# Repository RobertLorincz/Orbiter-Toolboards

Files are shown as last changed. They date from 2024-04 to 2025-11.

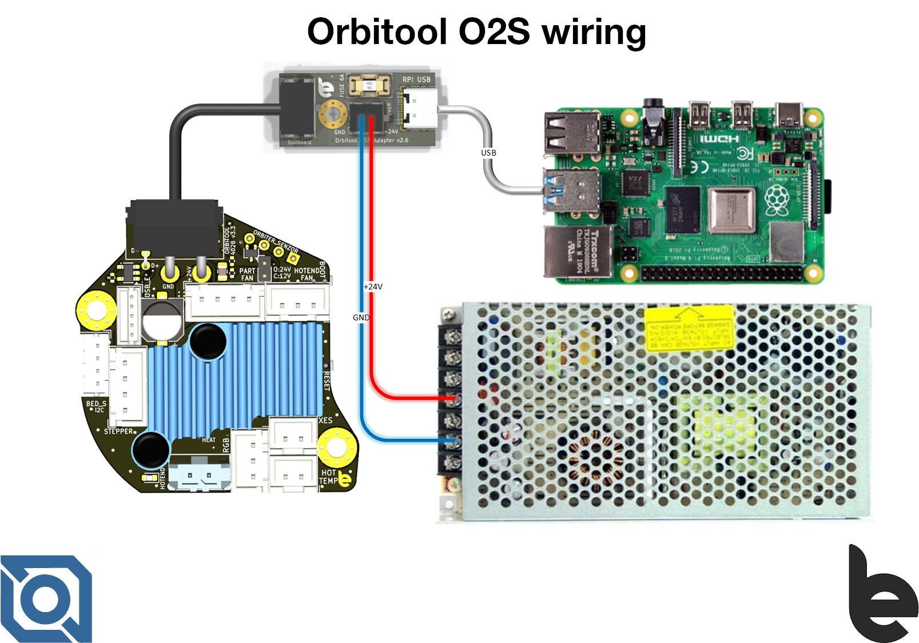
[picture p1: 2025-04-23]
Orbiter O2S Toolboard/Documentations/Orbitool O2S Wiring.jpg

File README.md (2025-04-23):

Should a tool-board magic smoke come out because of user error? Why?

Should a tool-board be destroyed by a fault in your 3D printer? Why?

My answer is NO! And this is what this tool-board is all about! 

We are hobbits, professionals and let’s face it, we do mistakes, and when the magic smoke shows up everybody is disappointed, even if we know it’s a user fault. In this board, I promise you the magic smoke is kept inside extremely tight!

Some of the main features:

•	Optimized for Orbiter v2, v2.5 and SO3 shape and features including orbiter sensor

•	STM32F042 / STM32F072 microcontroller running on 48MHz

•	Automotive USB communication with Raspberry PI

•	Onboard LIS2DW12 /ADXL345 accelerometer

•	TMC2209 extruder stepper driver

•	Direct connection to Orbiter v2 sensor

•	PWM controlled fan outputs

•	DC-DC converter based Hot-end fan driver, compatible with 12/24V fan types with RPM speed input signal

•	Hot-end temperature sensor input compatible with standard NTC or PT1000 temperature sensor types

•	I/O for bed level sensing

•	X-Stop sensor input

•	RGB LED driver output

•	Onboard temperature sensor

•	Advanced thermal management system

GOFUuGBbQAESqu3 (1)
O2 Toolboard
Orbitool USB Adapter housing

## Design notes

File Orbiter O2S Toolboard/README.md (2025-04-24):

This is the second revised version of the Orbiter O2 toolboard.

Some of the main features:

•	Optimized for Orbiter v2, v2.5 shape and features, including orbiter sensor

•	STM32F072 microcontroller running on 48MHz - full klipper support with automatic update possibility

•	Automotive USB communication with Raspberry PI

•	One auxiliary USB connector for bed scanner, nozzle camera, or other inteligent USB connected accessory

•	Onboard ADXL345 accelerometer

•	TMC2240 extruder stepper driver - for better thermal behavior

•	Direct connection to Orbiter v2 sensor

•	PWM 4,3,2 wire part fan output, compatible with 12/24V fan types with RPM speed input signal

•	DC-DC converter based Hot-end fan driver, compatible with 12/24V fan types with RPM speed input signal

•	Hot-end temperature sensor input compatible with standard NTC or PT1000 temperature sensor types

•	I2C for bed level sensing and scanning

•	X-Stop sensor input

•	RGB LED driver output

•	Onboard temperature sensor

•	Advanced thermal management system

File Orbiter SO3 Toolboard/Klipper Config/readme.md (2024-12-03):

Changes v2.2.6
- print cancel restores the printer idle timer to 10 min

Changes v2.2.5

- Included CANCEL macro for user using the sensor macros instead of their own macros
- Pausing printer due to runnout detection increases printer timeout to 3600s - 1h (configurable by pause_timeout); timeout set back to default ten minutes after print resume.
- improved temperature restore behavior
- Filament automatic unload after runnout can be disabled by variable disable_runout_unload.
- corrected some minor bugs and spelling
- messages sent to console shows SO3: prefix
- corrected RGB led incorrect color status for some failure cases

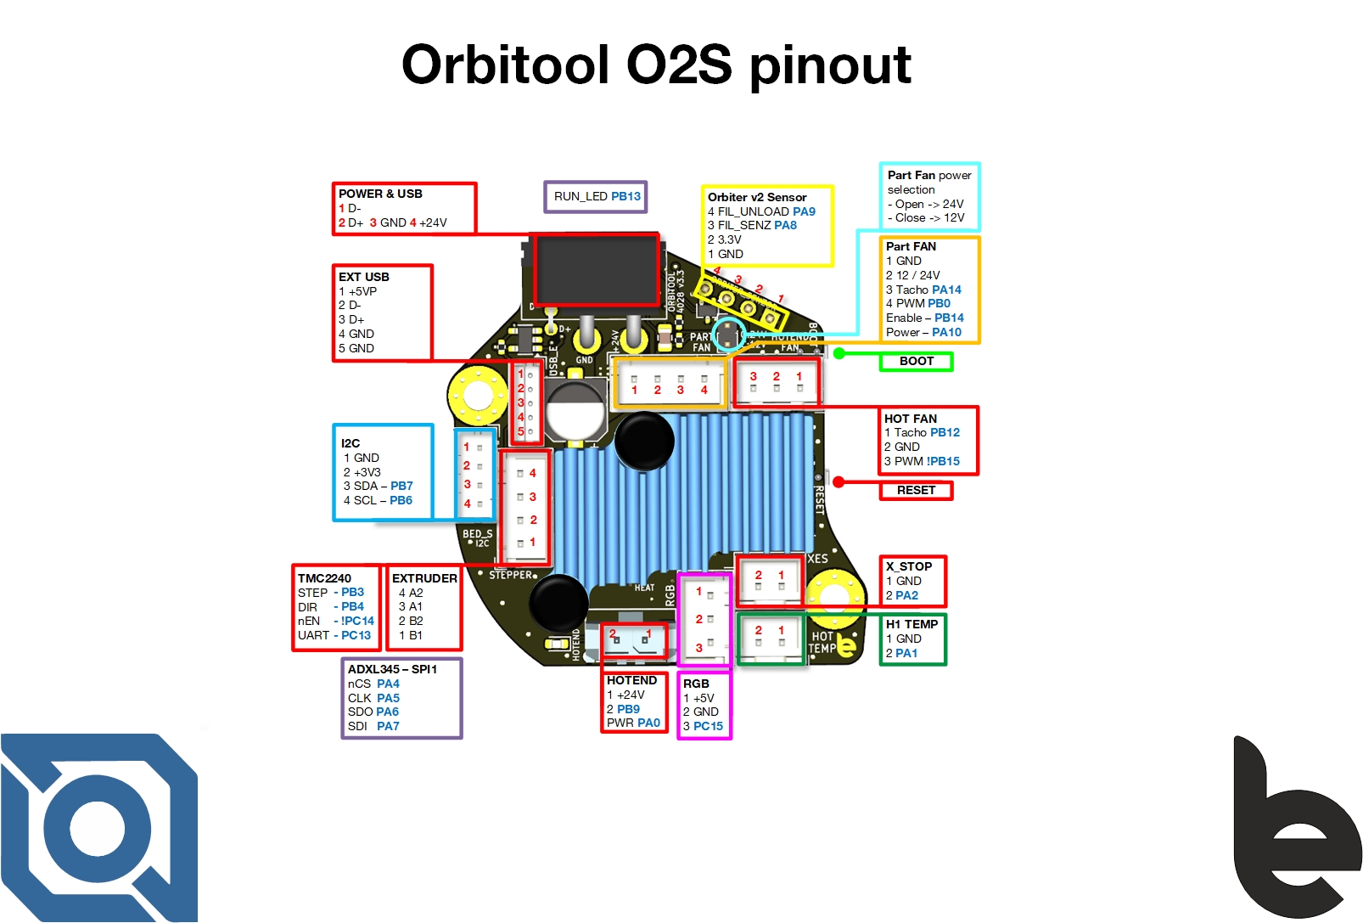
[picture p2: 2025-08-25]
Orbiter O2S Toolboard/Documentations/Orbitool O2S Pinout.jpg

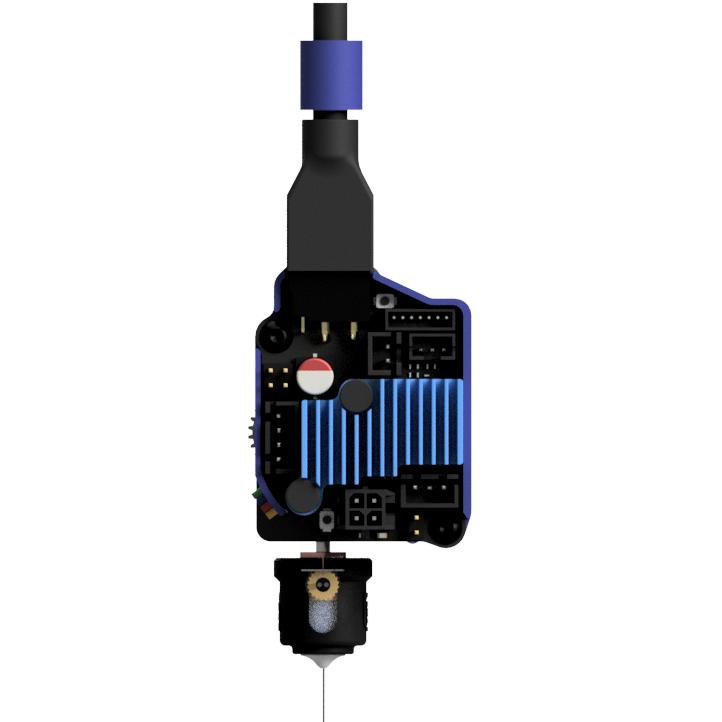
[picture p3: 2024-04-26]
Orbiter SO3 Toolboard/Pictures/Orbiter Smart LDO p3.png

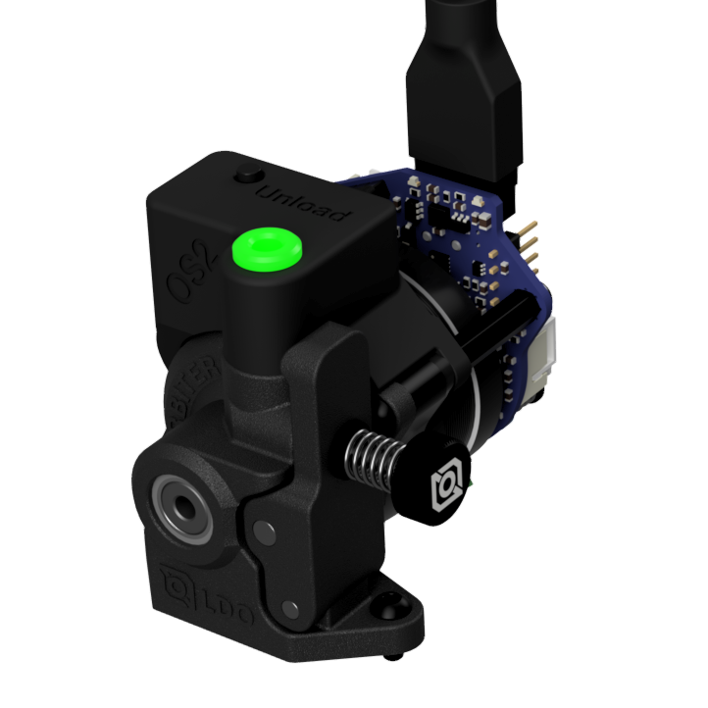
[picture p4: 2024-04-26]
Orbiter O2 Toolboard/Pictures/Orbiter v2 Toolboard v2.72 v151.png

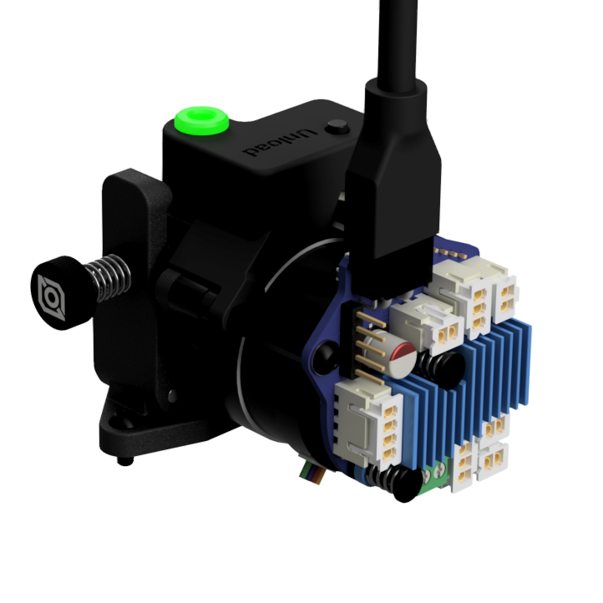
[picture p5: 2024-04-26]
Orbiter O2 Toolboard/Pictures/Orbiter v2 Toolboard v2.72 v15.png

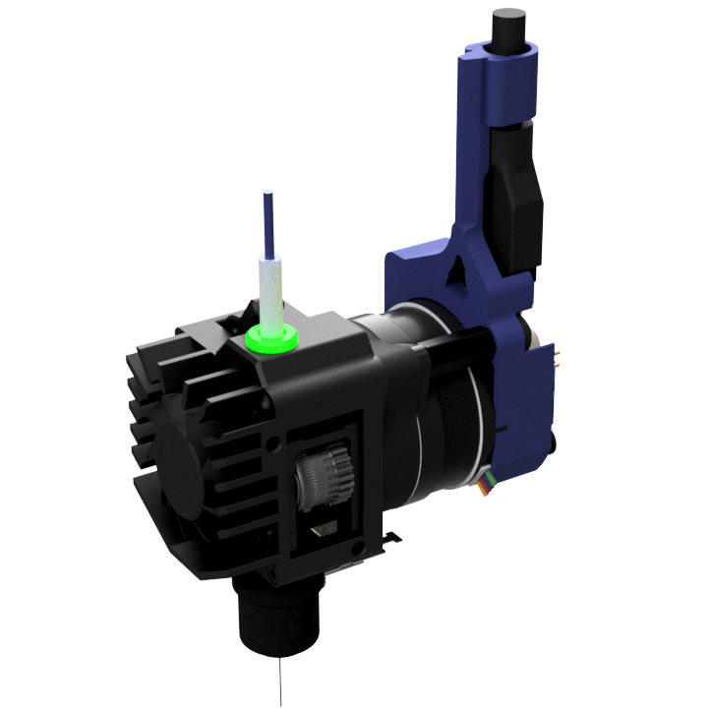
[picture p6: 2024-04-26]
Orbiter SO3 Toolboard/Pictures/Orbiter Smart LDO p2.png

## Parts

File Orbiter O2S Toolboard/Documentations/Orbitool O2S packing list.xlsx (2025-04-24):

Orbitool O2S toolboard pack list
Item | Description | Nr pieces / length | Part number | LCSC
1 | Orbitool O2S | 1 | v3.3
2 | USB adapter board | 1 | v3.0
3 | 24V USB cable | 150cm | v2
4 | 24V power supply cable | 50cm
5 | Short USB A to USB C cable | 30cm
6 | Orbiter Sensor connecting bridge | 1 |  | C2718488
7 | XH-2 pin connector housing | 2 | XHP-2 | C144401
8 | XH-3 pin connector housing | 2 | XHP-3 | C144402
9 | XH-4 pin connector housing | 2 | XHP-4 | C144403
10 | XH crimp pins | 25 | SXH-001T-P0.6N | C385122
11 | PH-4 connector housing | 1 | PHR-4 | C111514
12 | PH crimp pins | 10 | SPH-002T-P0.5S | C111515
13 | ZH-5 connector housing | 1 | ZHR-5 | C160378
14 | ZH crimp pins | 10 | SZH-002T-P0.5 | C246761
15 | Molex Micro-Fit 2 pin connector housing | 1 | 436450200 | C114089
16 | Molex Micro-Fit crimp pins | 5 | 430300001 | C259786
17 | 2mm Jumper | 2 |  | C5664
18 | M3 threaded aluminum spacer L=14mm | 2 | M3 L14
19 | M3 threaded aluminum spacer L=18mm | 2 | M3 L18
20 | M3 screw L = 8mm | 3 | M3x8
21 | Me screw L = 25 | 2 | M3x25
22 | M3 washers | 2
23 | M3 brass insert nut L=6mm | 2
23 | M3 nut | 2

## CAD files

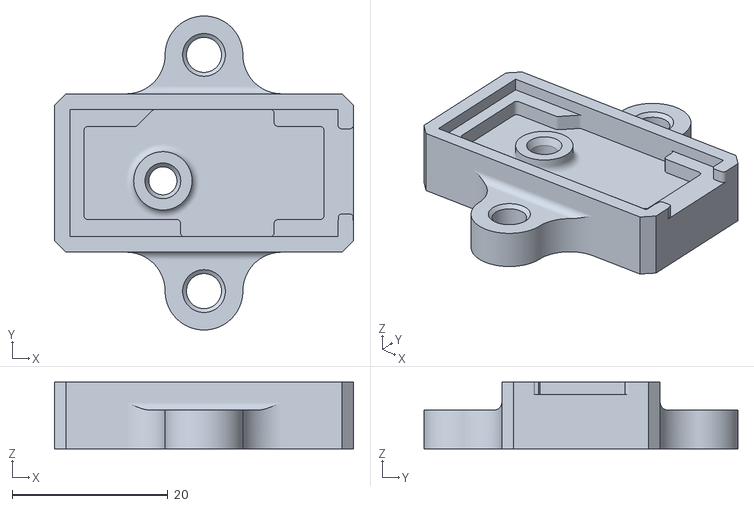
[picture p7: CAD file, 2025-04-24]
Orbiter O2 Toolboard/3D CAD/O2S USB Adaptor bracket.stl
38.4 x 40.4 x 8.60

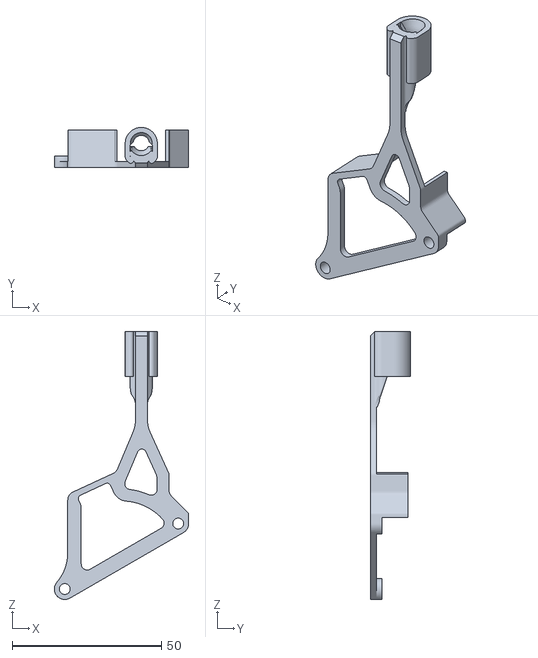
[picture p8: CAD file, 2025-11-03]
Orbiter O2S Toolboard/3D CAD/Orbitool O2S Wire restrain Straight.stl
44.9 x 13.4 x 89.7

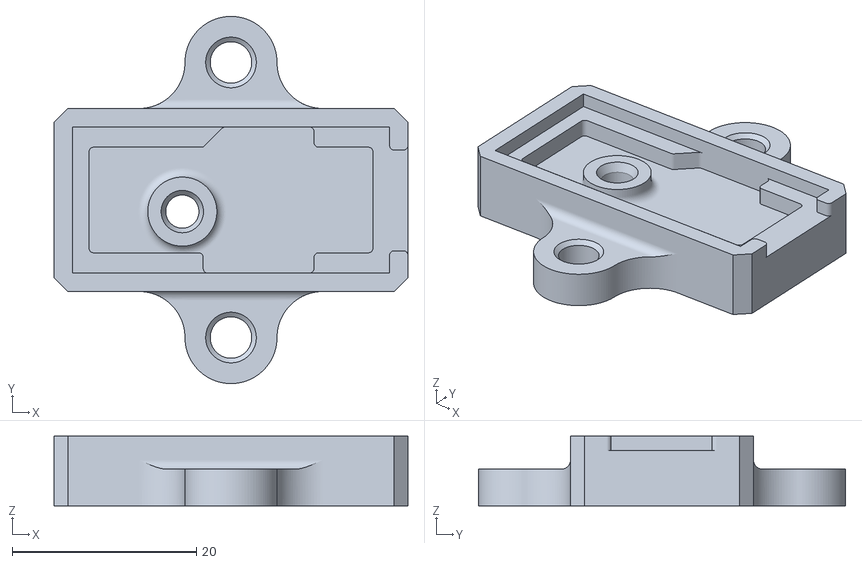
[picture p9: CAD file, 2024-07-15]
Orbiter SO3 Toolboard/3D CAD/USB Adaptor mount.stl
38.4 x 39.9 x 7.60

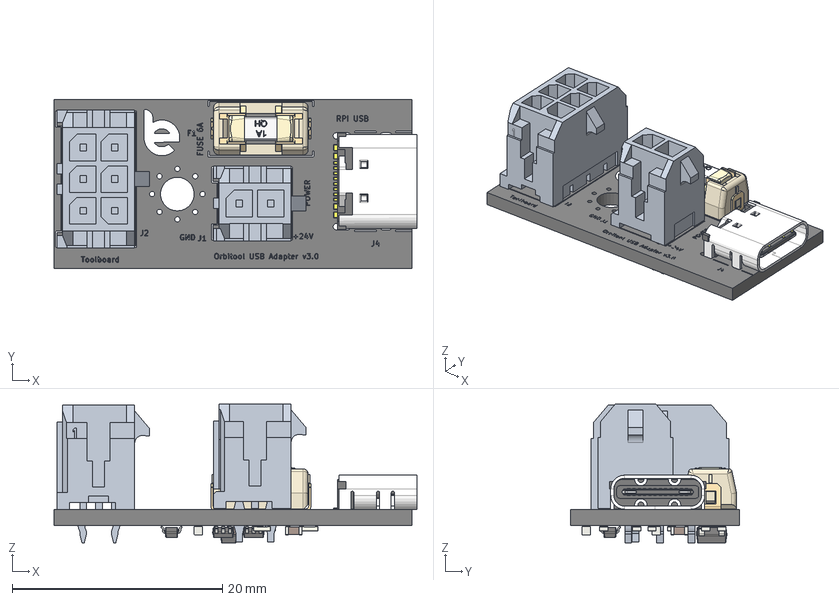
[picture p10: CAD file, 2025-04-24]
Orbiter O2 Toolboard/3D CAD/Orbitool O2S USB Adapter.step
34.5 x 16.1 x 13.2 mm
0679H1000-xxsingle fonts v2
Terminal
USB_type_C_smd_12p
SOT-323_SC-70
SOT-363_SC-70-6 x 2
R_0603_1608Metric x 7
C_0603_1608Metric x 4
SOT-23-5
Orbitool USB Adapter v3.0.1kicad_pc_20041120_silkscreen
Orbitool USB Adapter v3.0.1kicad_pc_20041120_PCB

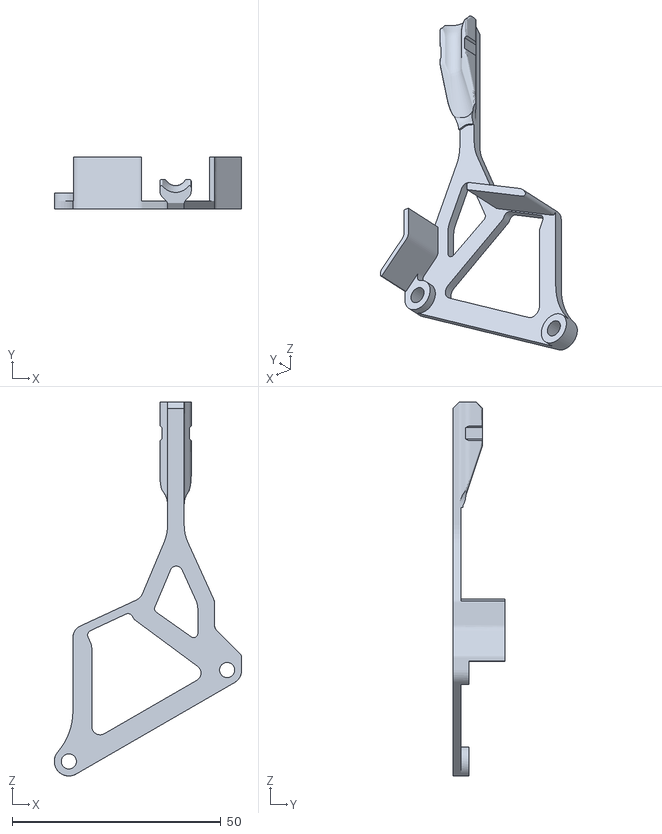
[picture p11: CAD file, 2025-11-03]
Orbiter O2S Toolboard/3D CAD/O2S WirerestrainBody.stl
44.9 x 12.5 x 89.7

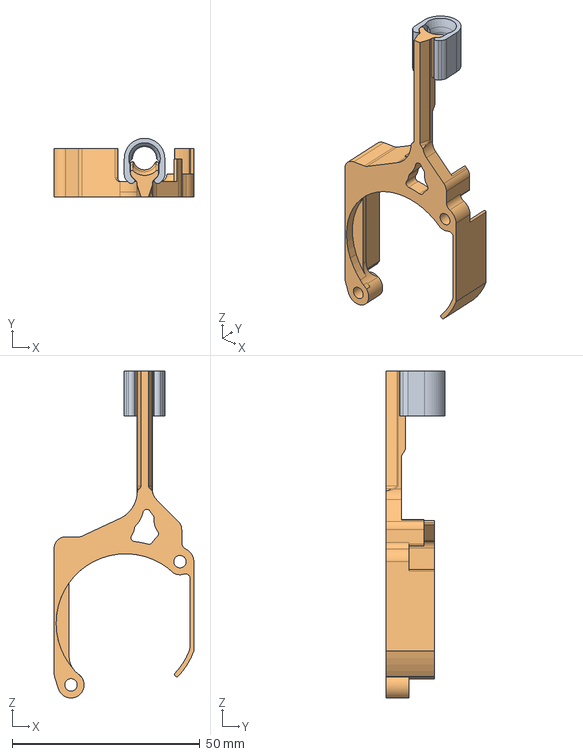
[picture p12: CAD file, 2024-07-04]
Orbiter SO3 Toolboard/3D CAD/SO3 Toolboard Bracket.step
37.2 x 15.6 x 87.1 mm
SO3_WireLock
SO3_WireRestrain

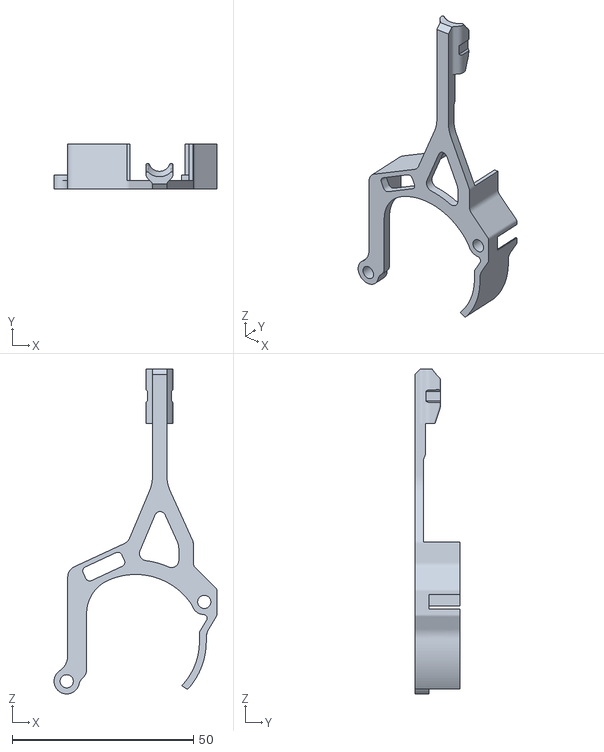
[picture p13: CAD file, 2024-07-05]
Orbiter O2 Toolboard/3D CAD/WirerestrainBracket.stl
44.9 x 12.5 x 89.7

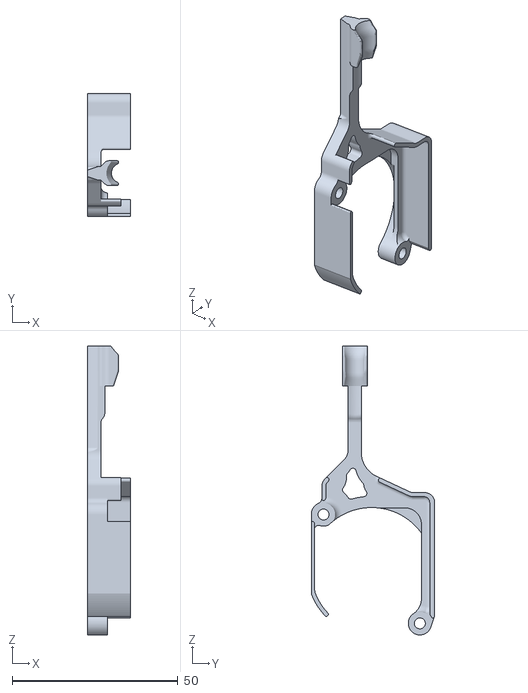
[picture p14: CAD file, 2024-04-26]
Orbiter SO3 Toolboard/3D CAD/SO3_WireRestrain.stl
12.9 x 37.2 x 87.1

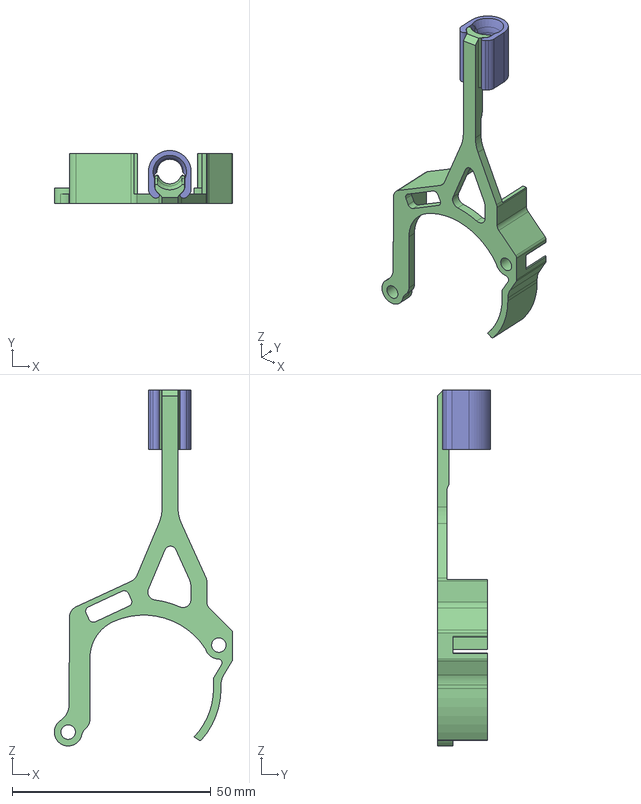
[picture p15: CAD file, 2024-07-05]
Orbiter O2 Toolboard/3D CAD/OBT2 Bracket Wire restrain.step
44.9 x 13.4 x 89.7 mm
WirerestrainBracket
Wirestrain_Lock v2

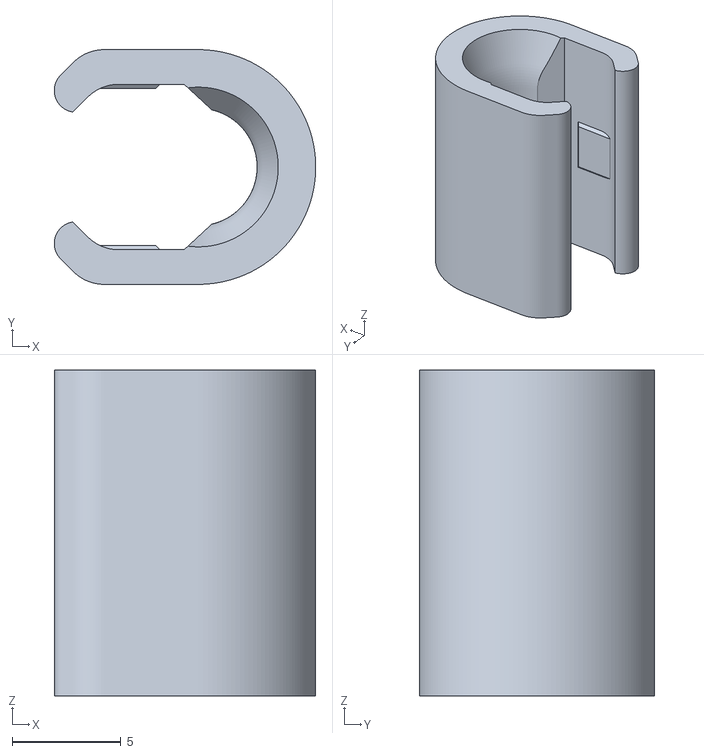
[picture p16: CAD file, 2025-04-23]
Orbiter O2S Toolboard/3D CAD/O2S Wirestrain_Lock.stl
12.0 x 10.8 x 15.0

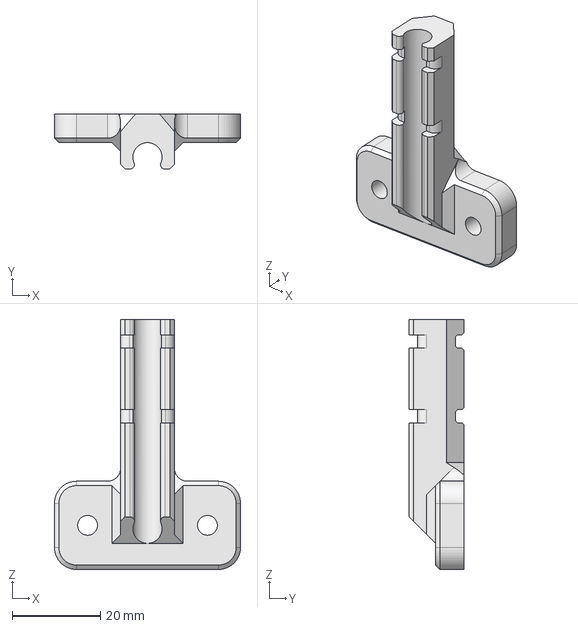
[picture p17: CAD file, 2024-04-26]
Orbiter SO3 Toolboard/3D CAD/Strain Releaser Frame v1.step
42.1 x 12.5 x 56.6 mm

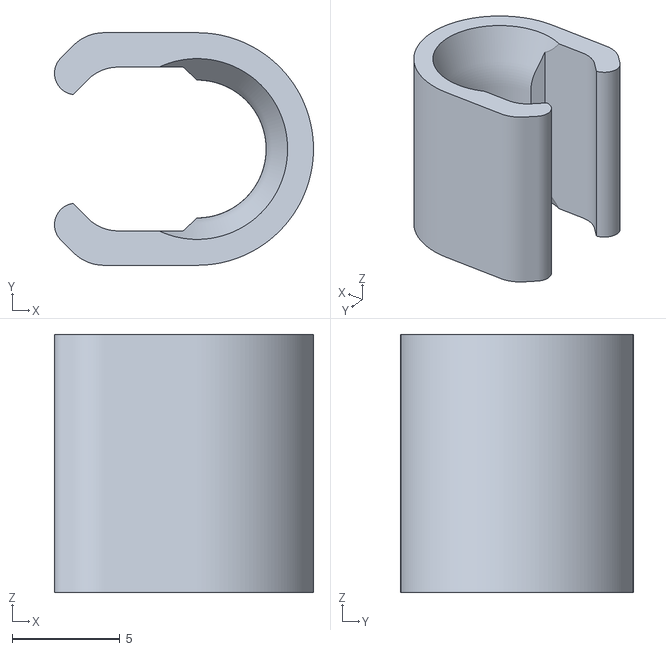
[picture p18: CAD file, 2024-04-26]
Orbiter SO3 Toolboard/3D CAD/SO3_WireLock v1.stl
12.0 x 10.8 x 12.0

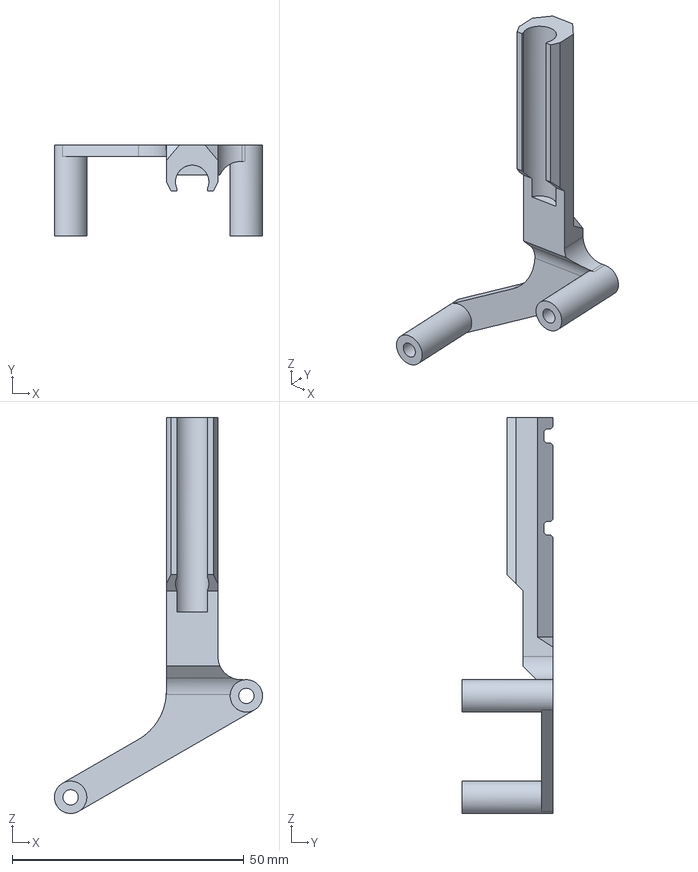
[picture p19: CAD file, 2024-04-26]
Orbiter O2 Toolboard/3D CAD/Strain Releaser v1.step
44.9 x 19.8 x 85.5 mm

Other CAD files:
Orbiter O2S Toolboard/3D CAD/Orbitool O2S Wire restrain.step
Orbiter O2 Toolboard/3D CAD/Orbiter v2 Sensor v4.1 LDO MJF v48.stl
Orbiter O2S Toolboard/3D CAD/Orbitool O2S USB Adapter.step
Orbiter O2 Toolboard/3D CAD/OBT2 Bracket Wire restrain.f3d
Orbiter O2 Toolboard/3D CAD/Strain Releaser Frame v1.stl
Orbiter O2 Toolboard/3D CAD/Strain Releaser v1.stl
Orbiter O2S Toolboard/3D CAD/Orbitool O2S USB Adapter.f3d
Orbiter O2S Toolboard/3D CAD/Orbitool O2S Wire restrain.f3d
Orbiter O2S Toolboard/3D CAD/Orbitool USB O2S v3.3.f3d
Orbiter SO3 Toolboard/3D CAD/Orbitool SO3.f3d
Orbiter SO3 Toolboard/3D CAD/Orbitool USB Adapter with mount.f3d
Orbiter SO3 Toolboard/3D CAD/Strain Releaser Frame v1.stl

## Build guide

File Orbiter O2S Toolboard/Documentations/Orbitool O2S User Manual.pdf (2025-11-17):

# Orbitool O2S

Should a tool-board magic smoke come out because of user error? Why?

Should a tool-board be destroyed by a fault in your 3D printer? Why?

My answer is NO! And this is what this toolboard is all about!

We are hobbyists and professionals, and let’s face it, we make mistakes, and when the magic smoke shows up, everybody is disappointed, even if we know it’s a user’s fault. In this board, I promise you the magic smoke is kept inside extremely tight!

Smokeless Features

- Optimized for Orbiter v2 shape and features and not only
- STM32F072 microcontroller running at 48MHz
- Automotive USB communication with a Raspberry Pi
- Second onboard USB port
- Onboard ADXL345 accelerometer
- TMC2240 extruder stepper driver
- Direct connection to the Orbiter v2 sensor
- 4 wire-controlled part fan output with configurable supply voltage
- DC-DC converter based hot-end fan driver, compatible with 12/24V fan types with RPM speed input signal
- Hot-end temperature sensor input compatible with standard NTC or PT1000 temperature sensor types
- I2C port for bed scanner
- X-Stop sensor input
- RGB LED driver output
- Onboard temperature sensor
- Advanced thermal management

Protection Features

- Active short-circuit protected Hotend output
- Active short circuit protected fan driver outputs
- Active protection circuit against reverse power supply connection
- Protection against loss of GND supply
- Analog and digital inputs protected against short to +24V supply voltage
- USB data lines are protected against short circuits to GND and +24V
- RGB LED power supply pin protected against short to GND
- EMI interference and ESD protection for all inputs and outputs
- Heater thermal runaway protection in case of a short between heater and sense thermistor wires

Author: Dr. Róbert Lőrincz

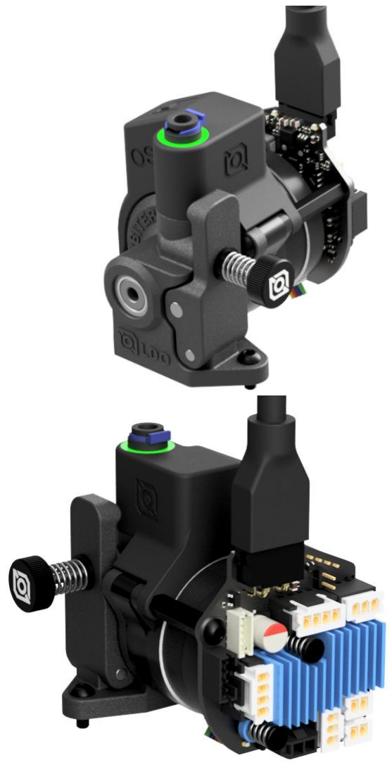
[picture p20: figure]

# 1 Block Diagram

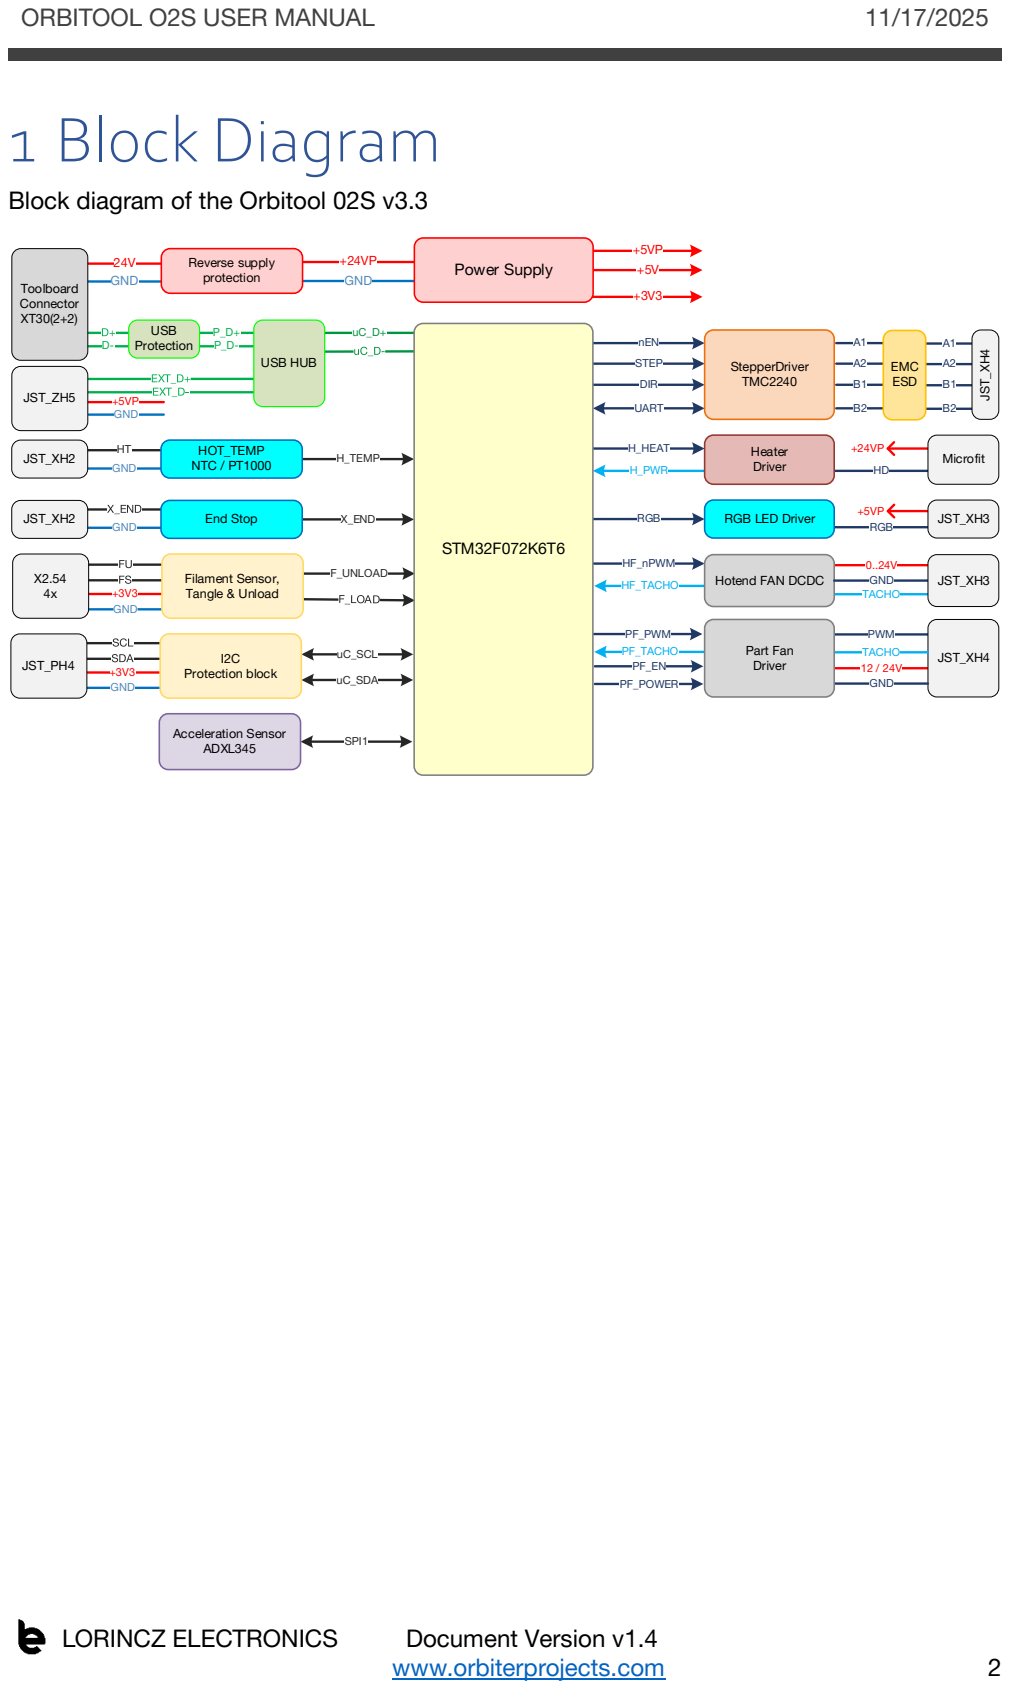
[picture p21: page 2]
ORBITOOL O2S USER MANUAL; LORINCZ ELECTRONICS; Document Version v1.4; www.orbiterprojects.com; nEN; STEP; DIR; UART; JST_XH⁴; EMC ESD; H_HEAT; H_PWR; Microfit Heater; Driver; StepperDriver TMC2240; RGB; +5VP RGB; HF_nPWM; HF_TACHO; TACHO; PF_PWM; PWM; JST_XH3; JST_XH4; 24V GND; GND; X_END; H_TEMP; F_UNLOAD; uC_SCL; uC_SDA GND; SPI1; Toolboard Connector XT30(2+2); JST_XH2; JST_PH4; Protection block; Filament Sensor, Tangle & Unload; End Stop; HOT_TEMP NTC / PT1000; Acceleration Sensor ADXL345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

Block diagram of the Orbitool 02S v3.3

RGB LED Driver

Hotend FAN DCDC

# 2 Pinout definition

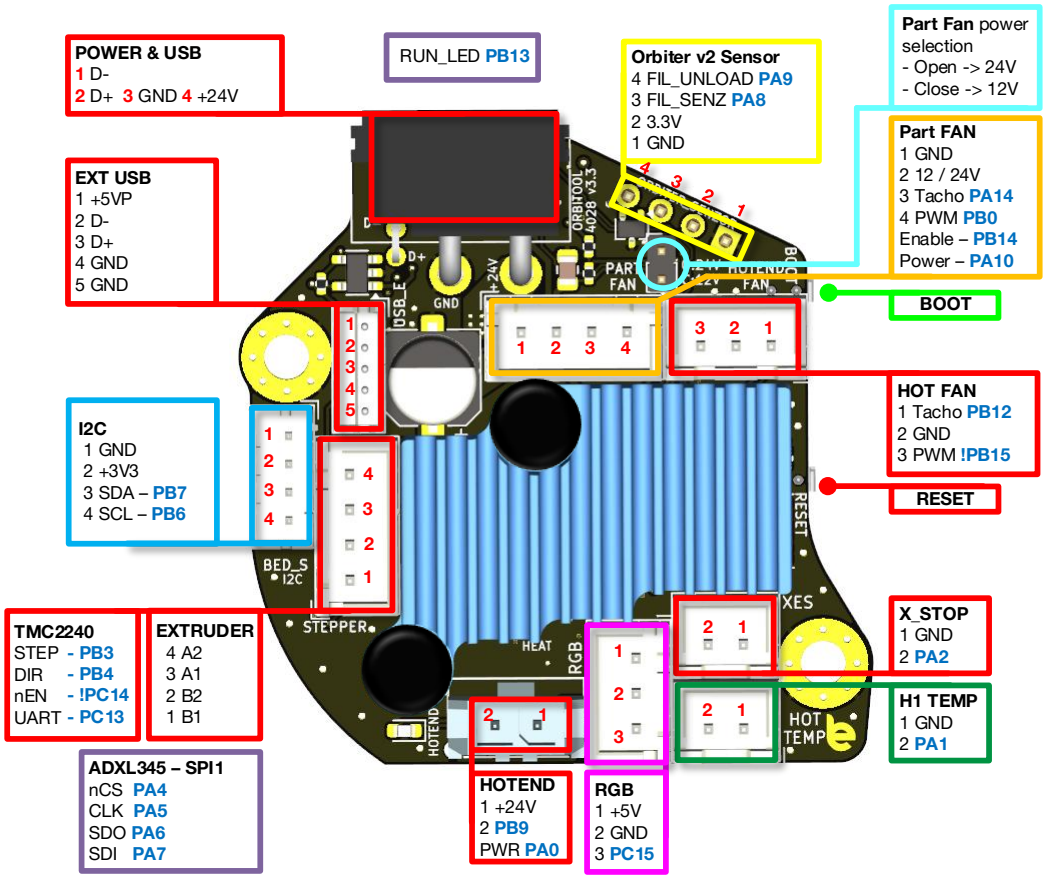
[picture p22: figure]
Part FAN 1 GND 2 12 / 24V 3 Tacho PA14 4 PWM PB0 Enable – PB14 Power – PA10; HOT FAN 1 Tacho PB12 2 GND 3 PWM !PB15; EXTRUDER 4 A2 3 A1 2 B2 1 B1; TMC2240 STEP DIR nEN UART; EXT USB 1 +5VP 2 D- 3 D+ 4 GND 5 GND; X_STOP 1 GND 2 PA2; H1 TEMP 1 GND 2 PA1; RGB 1 +5V 2 GND 3 PC15; HOTEND 1 +24V 2 PB9 PWR PA0; Orbiter v2 Sensor 4 FIL_UNLOAD PA9 3 FIL_SENZ PA8 2 3.3V 1 GND; ADXL345 – SPI1 nCS PA4 CLK PA5 SDO PA6 SDI PA7; BOOT; RESET; POWER & USB 1 D- 2 D+ 3 GND 4 +24V; Part Fan power selection - Open -> 24V - Close -> 12V; I2C 1 GND 2 +3V3 3 SDA – PB7 4 SCL – PB6; RUN_LED PB13

# 3 Features description

# 3.1 Introduction

For me, the electrical robustness of a design is part of the requirements. One of my main design goals was to integrate protection against common user errors and 3D printer defects.

In the end, nothing is more frustrating than powering up your new board and letting the magic smoke out. Even if it is due to user fault, the disappointment will still be present.

This design is based on automotive technology, where protection from all kinds of hazards is state-of-the-art a long time ago.

This document describes the main specific features of the tool-board.

Main changes compared to previous toolboard version v3.3:

- Secondary USB output for connection of a nozzle camera or bed level scanner, etc.
- Part fan supports 2, 3 and 4 wire fans with configurable power supply voltage. The power supply is able to deliver 2A of current, enabling the direct operation of the most powerful 4028 fans.
- I2C IO port for interconnection with I2C protocol sensors (like OrbiScan bed scanner). This port replaces the old BL_TOUCH connection of the previous board version
- Hotend heater connector changed from screw terminal to micro fit connector.
- Tool fan output has been removed, to make space for the 4wire part fan interface.
- The microcontroller has been changed to STM32F072K6T6, with a larger flash memory allowing bootloader flashing and auto update directly from the Mainsail interface.
- Onboard accelerometer changed to ADXL345
- Stepper driver changed to TMC2240 which has lower thermal losses compared to TMC2209
- USB adapter protection circuit supplied from onboard 5.5V power supply, not relying anymore on the 5V supply from the RPI, making the USB communication more stable.

# 3.2Power supply concept

The board is supplied via an XT30 (2+2) connector, which includes +24V, GND, USB_DATA+ and USB_DATA- signals.

From the connector, the board is supplied via a reverse power supply protection circuit. This prevents tool-board damage. In the event of an accidental reversed supply by user error, the board will not start up and will behave like it’s not powered.

The microcontroller is supplied from a 3.3V LDO supplied from the onboard 5V DC-DC buck converter for the highest power supply efficiency and lowest possible power consumption.

The RGB LED and the external USB port are supplied from a short-to-GND protected power supply.

# 3.3USB communication interface

The tool-board is equipped with an automotive grade USB interface. The main difference is the higher electrical robustness of the automotive USB, still maintaining the highest possible communication speed. Therefore, if the USB data lines are short-to-GND or up to +28V, it will not cause any destruction and will work properly after the short circuit is removed.

The same circuit offers protection in case of GND connection loss, which will lead to biasing all the communication signals to the supply positive line (in our case, +24V).

The USB interface of the Raspberry Pi is not robust against these electrical hazards that may occur in a 3D printer. Therefore, the tool-board shall be supplied and connected to the Raspberry Pi using the supplied adapter board, which has onboard protection circuits to protect the Raspberry Pi USB port.

The next picture presents the tool-board wiring connection principle.

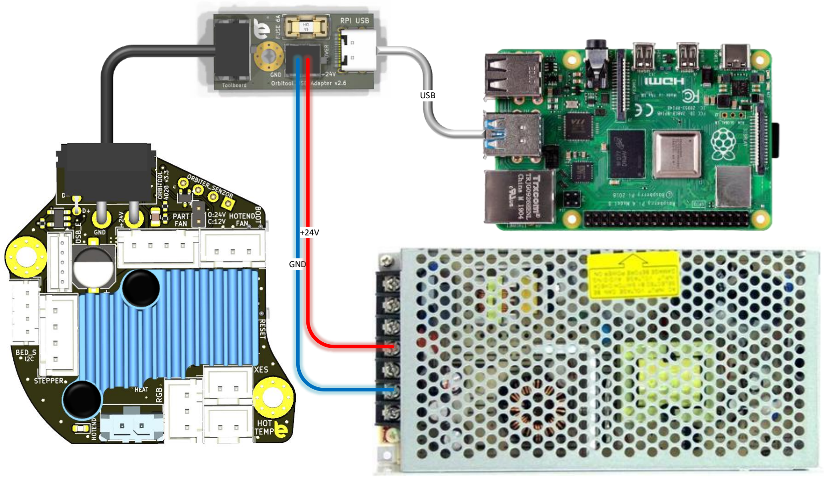
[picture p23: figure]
GND; USB

# 3.4Hot-end temperature sensor

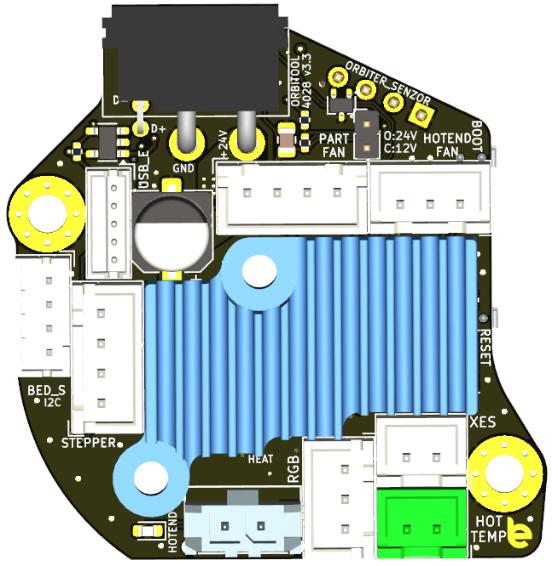
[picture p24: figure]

The hot-end input circuit accepts two types of thermistors: 100k NTC type similar to the ATC Semitec 104GT-2 and PT1000.

Pull-up resistor value: 2200Ω.

The sensor input is protected against short circuits to GND and supply voltage of 24V.

The GND connection of the sensor is current limited to avoid thermal runaway of the hotend in the event of a short circuit between the sensor and heater wires.

# 3.5Driver circuit for hot-end heater

The hot-end heater driver circuit is implemented with
active protection against short circuits.

The circuit measures the heater current and in case the current rises over a predefined threshold iOC_HOT, it switches off the heater MOSFET until the next PWM cycle to prevent damage.

The heater max power shall be limited to 99.5%,
meaning | max_power: 0.995 | to avoid the driver
getting stuck in protection mode due to an unlikely event of a fake error detection.

The heater current is fed to Klipper, which can

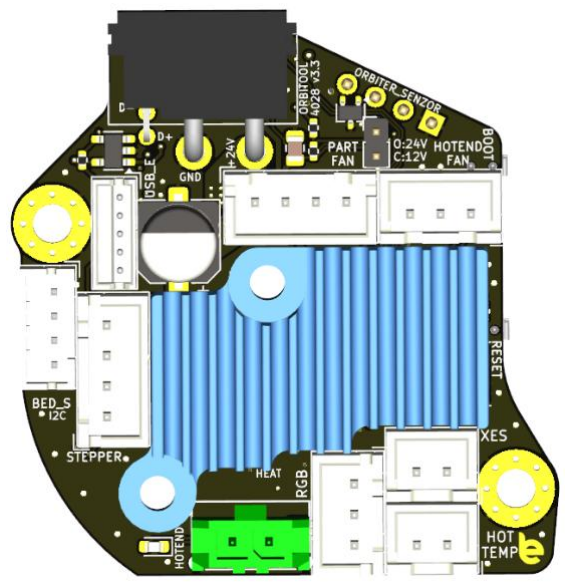
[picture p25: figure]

calculate the actual power consumption of the heater element. This can be used to detect failures of the heater element, like a short circuit or a loss of heating power.

You may say yes; other boards also have protection with onboard fuses. Well, that is simply not enough to protect MOSFETs from being damaged because fuses have a long reaction time, about 1~2s. Their mission is to protect the circuit from catching fire in case of a defect, but it cannot protect the heater driver MOSFET from getting destroyed. This active protection reacts within 10ms, ensuring the driver stage is switched off before it gets damaged due to a short circuit or overload event.

To display the actual power of the heater, include the following section:

The hot-end power or current can be displayed based on preference. The power is calculated considering a 24V power supply.

To improve the heater power calculation accuracy, the heater PWM is forced to 100Hz (instead of the 10Hz default of Klipper).

It is highly recommended to use ferrules to connect the heater wires to the tool-board screw terminal block.

# 3.6Part fan driver

The part fan connector supports the classical two or three wire fans, and four wire fans.

It can even drive the most powerful 4028 fans supplied by 12V.

The fan driver is based on a powerful 2A capable DC-DC converter circuit. The part fan is directly driven by a DC voltage instead of PWM. This reduces the fan noise caused by the PWM
chopping.

The power supply level of the part fan can be

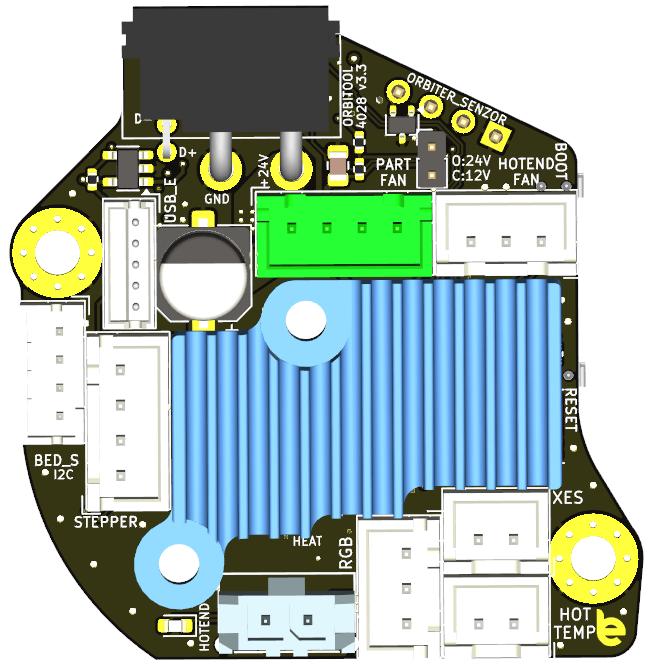
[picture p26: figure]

selected by the small 2mm jumper near the part fan connector as follows:

- Jumper open -> part fan supplied by 24V
- Jumper closed -> part fan supplied by 12V

Connector pins definition:

1- GND
2- 12/24V – positive supply for 2 and 3 wire fans 3- Tacho – speed signal
4- PWM for 4 wire fans

The fan driver has an enable signal connected to PB14.

3.6.1 Two wire fan connection and configuration

A regular two wire fan should be connected as follows:

- Negative terminal of the fan to pin number 1 – GND
- Positive terminal of the fan to pin number 2

Note: Pin number 4 – PWM is only used for 4 wire fans.

Warning: Please make sure the correct fan voltage is selected by the part fan voltage selection jumper. Supplying a 12V fan with 24V might damage the fan.

Since the driver applies a DC voltage instead of a PWM there could be a minimum voltage needed for the fan to start up.

This minimum value shall be defined experimentally (example: off_below: 0.2).

Klipper configuration example:

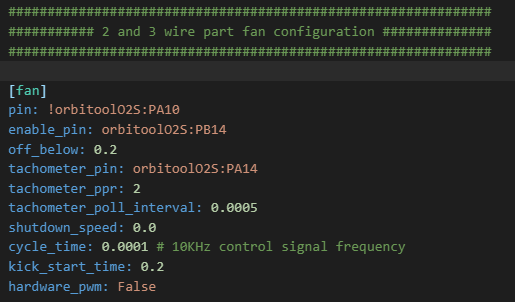
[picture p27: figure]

Note: The PWM frequency (cycle_time = 0.001) has nothing to do with the fan control. It is related to the fan control circuit, which is designed for a command signal of 10Khz.

3.6.2 Three wire fan connection and configuration

A three-wire fan should be connected as follows:

- Negative terminal of the fan to pin number 1 – GND
- Positive terminal of the fan to pin number 2 – 12/24V
- RPM terminal of the fan to pin number 3 - Tacho

Note: Pin number 4 – PWM is only used for 4 wire fans

Warning: Please make sure the correct fan voltage is selected by the part fan voltage selection jumper. Supplying a 12V fan with 24V might damage the fan.

Since the driver applies a DC voltage instead of a PWM there could be a minimum voltage needed for the fan to startup.

This minimum value shall be defined experimentally (example: off_below: 0.2).

Klipper configuration example:

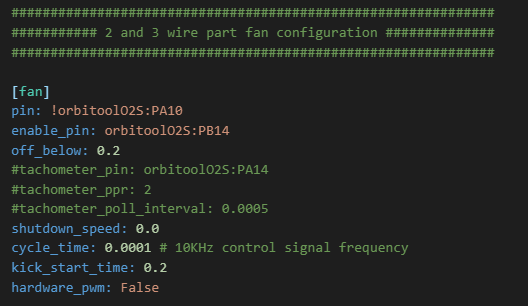
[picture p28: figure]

Note: The PWM frequency (cycle_time = 0.001) has nothing to do with the fan control. It is related to the fan control circuit, which is designed for a command signal of 10Khz.

3.6.3 Four wire fan connection and configuration

A four-wire fan should be connected as follows:

- Negative terminal of the fan to pin number 1 – GND
- Positive terminal of the fan to pin number 2 – 12/24V
- RPM terminal of the fan pin to number 3 – Tacho
- Speed control terminal of the fan to pin number 4 - PWM

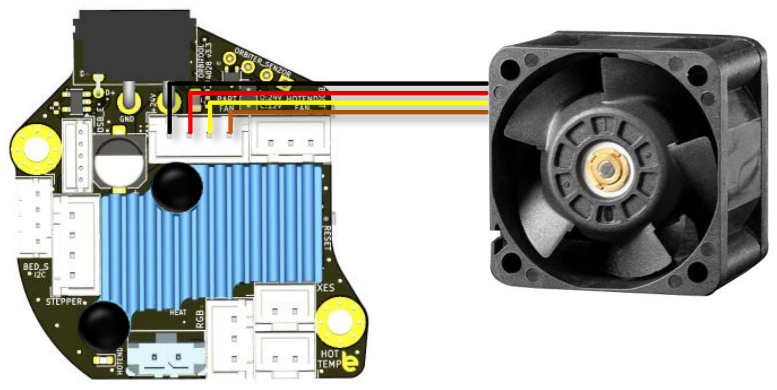
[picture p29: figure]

Note: Wire colors might be different, please consult the fan manufacturer documentation for details.

Warning: Please make sure the correct fan voltage is selected by the part fan voltage selection jumper. Supplying a 12V fan with 24V might permanently damage the fan.

Klipper configuration example:

Check out the fan datasheet for the correct speed control PWM frequency, most fans are working with 25Khz but it is not a universal standard.

3.6.4 Part fan supply voltage configuration

It is very important that the voltage selection jumper is fitted according to the used part fan.

A small 2mm jumper placed near the part fan connector selects the part fan supply voltage as follows:

- Open - 24V fan type
- Closed – 12V fan type

Be aware that supplying a 12V fan with 24V might permanently damage the fan!

# 3.7 Hot-end fan output

The hot-end fan circuit is implemented using a microcontroller-controlled DC-DC converter.

PWM control of three wire fans will destroy the speed signal. PWM (Pulse Width Modulation) control means switching on and off the fan power supply several times every second. This means there are moments when the fan is actually not supplied with power. In those moments, the speed sensing electronic circuit is not supplied, therefore it cannot generate a reliable speed signal. Practically, the PWM signal will be superimposed over the speed signal.

Another advantage of this control circuit is the
possibility of limiting the maximum voltage
according to the fan type the user has.

This output supports 12V or 24V fan types configured by the max power value in the fan configuration section:

- 12V fan – max_power: 0.5
- 24V fan – max_power: 1.0

Since the fan driver is based on a DC-DC converter, the PWM frequency required for correct operation is defined by the converter design, not by fan properties. Fan PWM speed control frequency shall be set to 10Khz, cycle time = 0.0001 – do not change this to a lower frequency.

Based on a specific printer design, the maximum power can be limited to reduce fan noise. Increase this to a higher level in case you experience hot end clogs.

The connection of a three-wire fan should respect the following connection scheme:

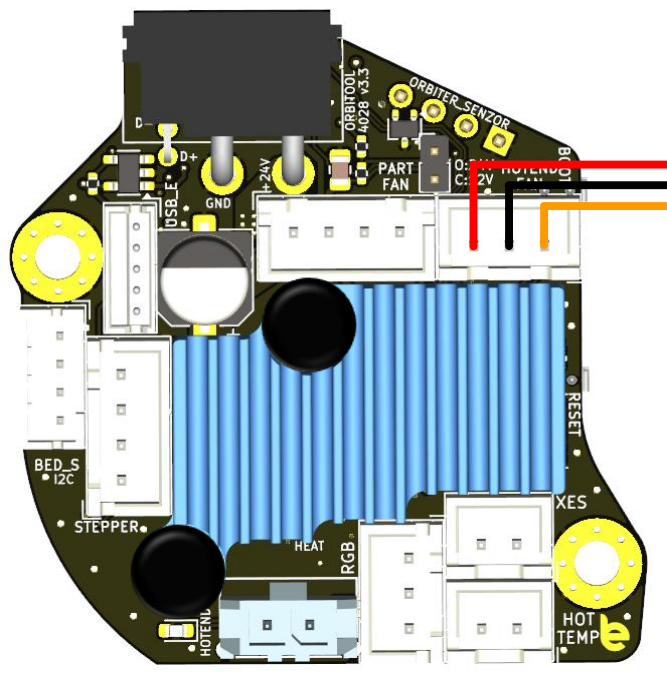
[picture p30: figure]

When a two-wire fan is connected, the orange wire shall be omitted and the pin left unconnected and the tachometer related configurations shall be commented out.

Klipper configuration example:

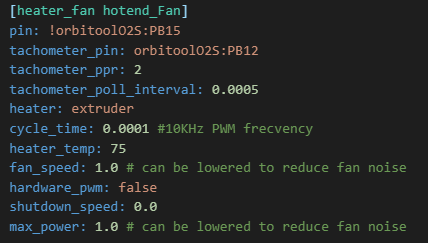
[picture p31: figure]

Note: The PWM frequency (cycle_time = 0.0001) has nothing to do with the fan control. It is related to the fan control circuit, which is designed for a command signal of 10Khz.

When a toolboard cooling fan is used, it is recommended to connect it together with the hotend fan as follows:

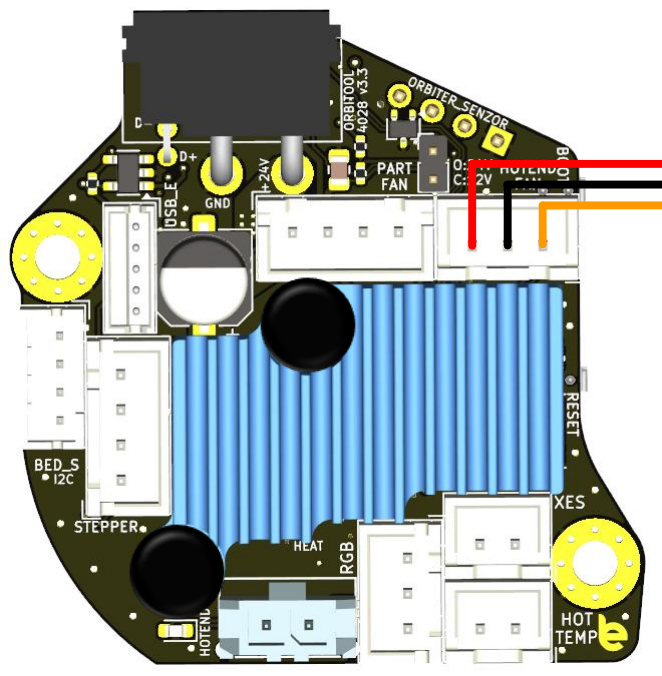
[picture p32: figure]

Hotend fan

Toolboard fan

# 3.8 Extruder stepper driver

The onboard stepper driver type is TMC2240, this has reduced power loss compared to the TMC2209, therefore the board has better thermal behavior and can be used with lower current limitation in a hot chamber.

Pinout of the extruder stepper connector:

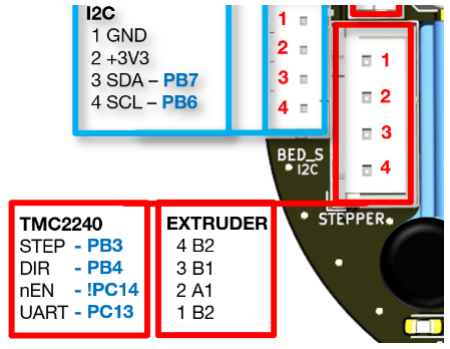
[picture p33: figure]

The stepper driver configuration is part of the extruder configuration, in this section, only the stepper driver related parts are defined.

Klipper configuration example:

# 3.9 ADXL345 Accelerometer

The toolboard is equipped with ADXL345 accelerometer connected to SPI1 of the microcontroller.

Klipper configuration example:

# 3.10 I2C interface

The onboard I2C port can be used to connect any type of external sensors with I2C communication protocol, like load cells, temperature sensors, eddy current based bed scanners (like Orbiscan or BTT Eddy Coil), etc.

The I2C bus name is: i2c1

The next picture presents a configuration example of an eddy current bed scanner:

# 3.11 Additional USB port

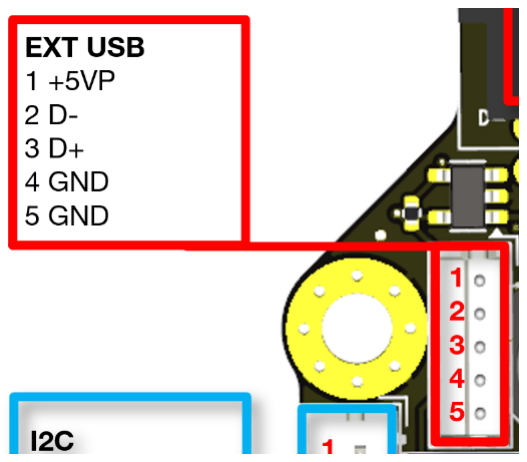
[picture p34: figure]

The additional onboard USB port is designed to support the USB1.0 protocol (12Mbit/s).

This USB port can be used to connect bed surface scanners like Beacon, Cartographer, BTT eddy with USB or a nozzle camera.

Note pin 4 and 5 are GND connections. The aim is that Pin 4 is used to connect the black USB wire and pin 5 to connect the USB cable shield. However, it is not mandatory to use both GND pins. The black wire and the USB cable shield can be tied together and connected to either of the GND pins.

# 3.12 Thermal considerations

A closed printer chamber requires tool-board operation in high ambient temperature conditions. In addition, this tool-board is mounted on the backside of the stepper motor, which transfers a considerable amount of heat. Therefore, the circuits of this tool-board are designed to have low temperature drift and efficient thermal management to make sure none of the components heat up over their maximum allowed operating temperature.

I performed lots of thermal simulations using finite element simulations and real-life measurements using a Flir thermal camera.

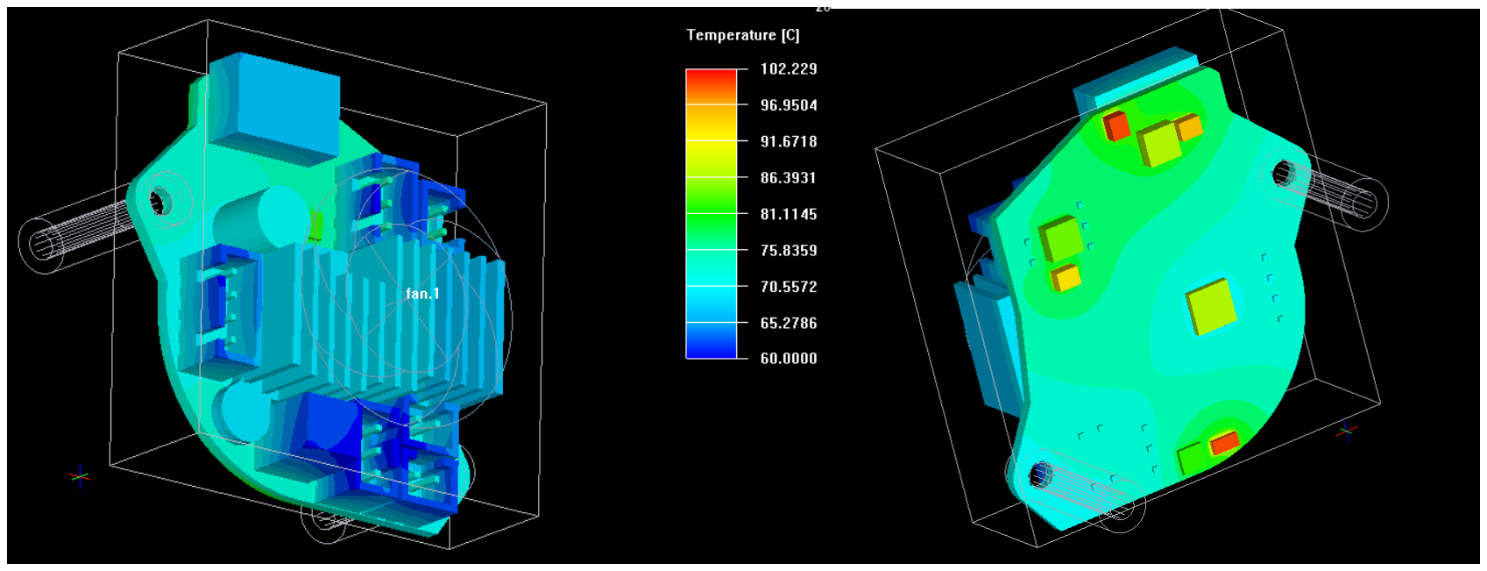
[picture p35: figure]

The simulation results show that in a 60°C chamber temperature environment, the tool-board components do not heat over their maximum junction temperature rating.

To reduce heat transfer from the stepper towards the tool-board a minimum distance of 4-5 mm shall be maintained. Orbiter v2 and v2.5 equipped with the LDO-36STH20-1004AHG stepper and the Orbiter smart sensor, standoffs with 18 mm length is recommended. This way, the distance between the toolboard PCB and the stepper back side is about 4-5 mm.

Without the Orbiter smart sensor, the standoff length shall be minimum 20 mm.

The toolboard is designed for passive cooling,
but even with the most optimized thermal
design, | stepper | current | derating | over

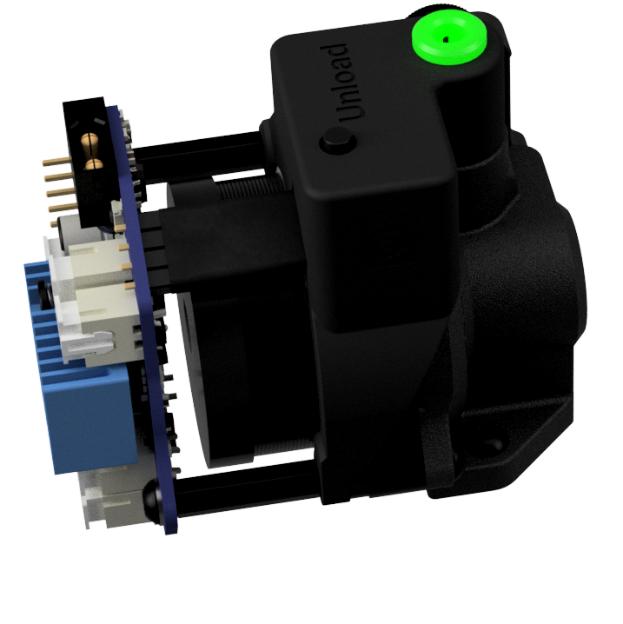
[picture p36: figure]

temperature still applies. This is mainly because there is simply not enough space for a bigger heatsink. Even if the heatsink size were doubled, it would still not be enough.

Therefore, we have two possible solutions:

1. Reduce stepper current for high ambient temperature operation. Example down to 0.55A for chamber temperature above 60°C.
2. Use active cooling to improve the thermal behavior. Adding a small 20x20mm or 25x25mm fan on the back of the toolboard that blows air toward the heatsink will
| improve a lot.

# 4 Microcontroller programming

1. Connect the board to the host Raspberry Pi via a USB adapter cable.

### 2. This step depends on whether your board has firmware on it or not:

a) If your board is pre-flashed with Klipper, first must enter DFU mode as follows:
- press the BOOT and RESET buttons,
- release the RESET while keeping the BOOT button pressed,
- release the BOOT button after about three seconds.
b) If your board is a new, un-flashed board:
- The MCU is already in DFU mode; confirm this at step 4

BOOT

RESET

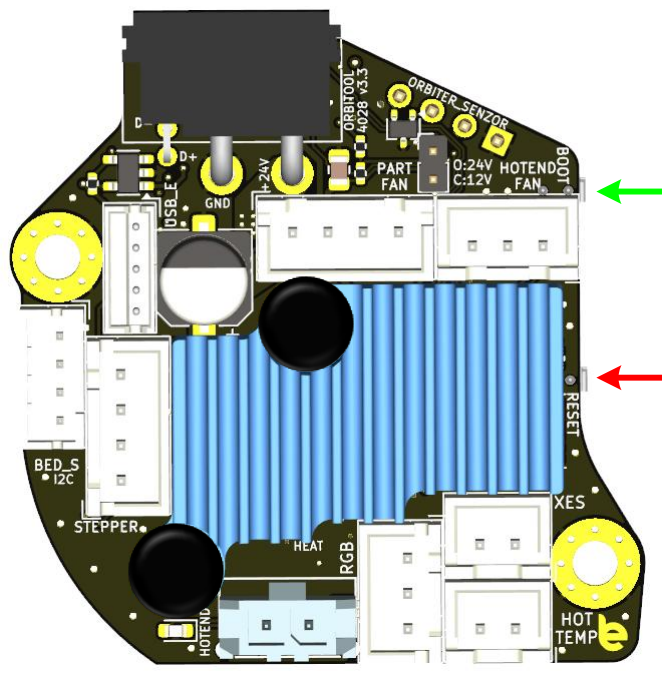
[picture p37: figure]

### 3. Connect to your host Raspberry Pi via SSH 4. Run lsusb from the command prompt

- Make sure you see an STM32 in DFU mode listed

### 5. Run dfu-util --list from the command prompt

- note the text inside the [xxxx:yyyy] (default is -> 0483:df11)

### 6. Run cd ~/klipper from the command line to enter the Klipper directory 7. Run make menuconfig settings should be:

- Cristal oscillator – 12Mhz

- Set custom USB ID to Orbitool_O2S
- Hit Q to Exit and Save

### 8. Run make clean to clean up the make environment 9. Run make flash FLASH_DEVICE=0483:df11

If you encounter some error at the end but still have the message of File downloaded successfully, you are good to proceed to the next step.

### 10. Press the RESET button to restart the MCU and enter normal operating mode 11. Run ls /dev/serial/by-id/* should return a device with

/dev/serial/by-id/usb-Klipper_stm32f072xb_Orbitool_O2S-if00
Copy this virtual serial port name to the Orbitool_O2S.cfg file in the MCU section

Manual definition of USB ID, flashing the MCU with Klipper will always result in the same serial ID.

Your tool-board should now be usable with Klipper. Use the example config file to get started. The best option is to copy the config file into the same directory as printer.cfg.
Add [include Orbitool_O2S.cfg] to the beginning of your printer.cfg to include the file. Comment out the unused I/O features of the OrbitoolO2S config section.

# 5 Assembly instructions

Based on the user setup, we can have several assembly combinations, as described below. As a recommendation, some kind of bracket with strain release for the USB cable is a must. Fixing the cable is necessary to prevent constant bending forces over the PCB during printhead movements. Even if the forces are not very high, it still stresses the PCB, and it could develop component or solder cracks. A well-designed strain release will avoid this issue.

# 5.1Orbiter v2 + Orbitool + Bracket

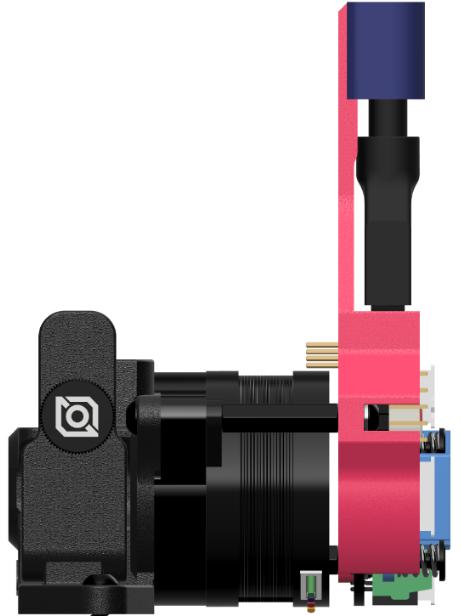
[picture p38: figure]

Mount the two M3 L=18mm standoffs to the Orbiter v2 stepper’s backside.

Print the braket and the wire lock (downloadable from GitHub). (https://github.com/RobertLorincz/Orbiter-Toolboards/tree/1304b2f8248f8c9e3053d22b78a8e4f7158f06ad/Orbiter%20O2S%20Toolboard/3D%20CAD)

Insert the toolboard into the bracket, and using the two M3 L=8 mm and two washers fix it to the two standoffs.

Insert the USB cable and fix it into place using the printed wire lock.

# 5.2 Orbiter v2 + Orbitool

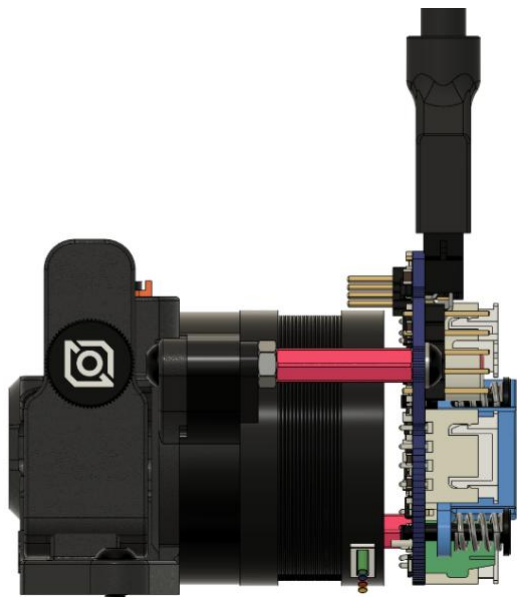
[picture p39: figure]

Change the two screws holding the Orbiter v2 together with the longer ones provided in the toolboard package (M3 L=25mm).

Add two M3 nuts over the screws on backside of the stepper, after which mount the two M3 L=18mm standoffs as shown in the picture.

Attach the toolboard and secure it in place with the M3 L=8mm screw sets and washers provided in the toolboard kit.

# 5.3Orbiter v2 + Orbitool + Orbiter sensor

Mount the Orbiter sensor over the top of the
Orbiter v2, using the two longer M3 screw sets provided in the sensor kit.

Insert the small interconnection part between the sensor and the toolboard into the sensor connector.

Screw on the two M3 standoffs with 18mm length over the sensor backside.

Attach the toolboard and secure it in place with the M3 L=8mm screw sets and washers provided in the toolboard kit.

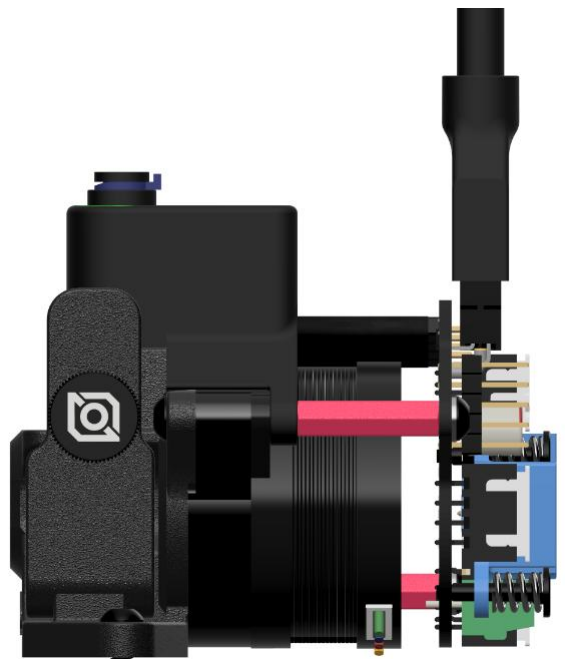
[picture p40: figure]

# 5.4 Orbiter v2 + Orbitool + sensor + bracket

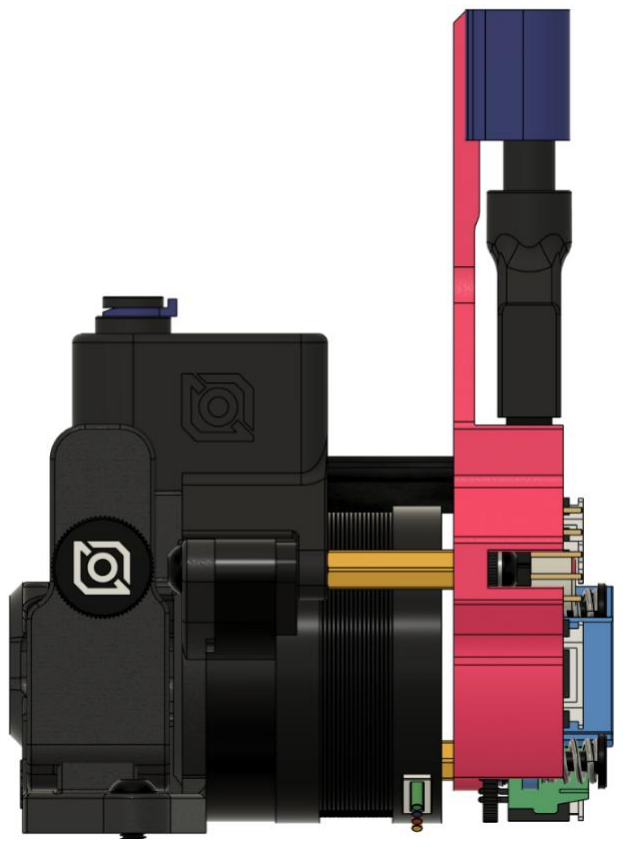
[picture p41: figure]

Mount the Orbiter sensor over the top of the Orbiter
v2, using the two longer M3 screw sets provided in the sensor kit.

Print the bracket and the wire lock (downloadable from GitHub). (https://github.com/RobertLorincz/Orbiter-Toolboards/tree/1304b2f8248f8c9e3053d22b78a8e4f7158f06ad/Orbiter%20O2S%20Toolboard/3D%20CAD)

Insert the small interconnection part between the sensor and the toolboard into the sensor connector.

Screw on the two M3 standoffs with 14mm length over the sensor backside.

Insert the toolboard into the bracket, and using the two M3 L=8 mm and two washers, fix it to the two standoffs.

Insert the USB cable and fix it into place using the printed wire lock.

# 5.5USB adapter board bracket

To fix the small USB adapter board to the printer frame, you may use my simple mount, as shown in the next picture. All you need is to print the mount, an M3 heat insert (L = 4~5 mm), and an M3 screw (L = 6~8 mm). The PCB mount can be fixed to the printer frame using two M3 screws and nuts, or attach it simply using strong foam tape.

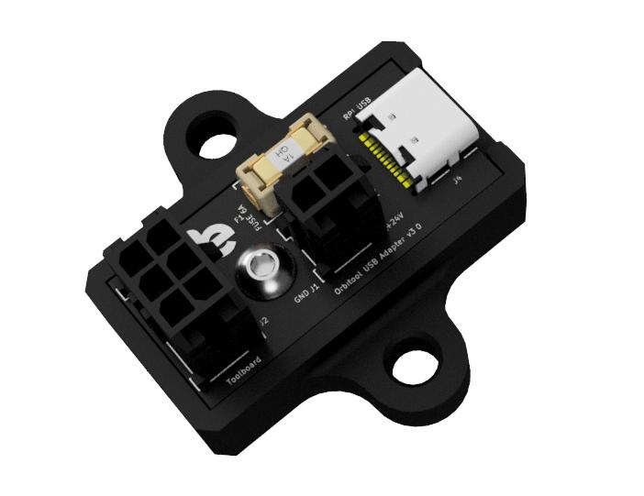
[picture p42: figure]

The new USB adapter board version 3.0 is an improved version compared to the last version, v2.72. It has an onboard 5V regulator that supplies the onboard USB protection circuit. This means the board is not relying anymore to receive a proper 5V supply voltage via the USB connector, resulting in more reliable USB communication, less probability of toolboard disconnection due to noise or instability of the 5V power supplied via the Raspberry PI USB connector.

# 5.6 Toolboard pack list

Orbitool O2S toolboard pack list
Item | Description | Nr pieces / length | Part number | LCSC
1 | Orbitool O2S | 1 | v3.3
2 | USB adapter board | 1 | v3.0
3 | 24V USB cable | 150cm | v2
4 | 24V power supply cable | 50cm
5 | Short USB A to USB C cable | 30cm
6 | Orbiter Sensor connecting bridge | 1 | | C2718488
7 | XH-2 pin connector housing | 2 | XHP-2 | C144401
8 | XH-3 pin connector housing | 2 | XHP-3 | C144402
9 | XH-4 pin connector housing | 2 | XHP-4 | C144403
10 | XH crimp pins | 25 | SXH-001T-P0.6N | C385122
11 | PH-4 connector housing | 1 | PHR-4 | C111514
12 | PH crimp pins | 10 | SPH-002T-P0.5S | C111515
13 | ZH-5 connector housing | 1 | ZHR-5 | C160378
14 | ZH crimp pins | 10 | SZH-002T-P0.5 | C246761
15 | Molex Micro-Fit 2 pin connector housing | 1 | 436450200 | C114089
16 | Molex Micro-Fit crimp pins | 5 | 430300001 | C259786
17 | 2mm Jumper | 2 | | C5664
18 | M3 threaded aluminum spacer L=14mm | 2 | M3 L14
19 | M3 threaded aluminum spacer L=18mm | 2 | M3 L18
20 | M3 screw L = 8mm | 3 | M3x8
21 | Me screw L = 25 | 2 | M3x25
22 | M3 washers | 2
23 | M3 brass insert nut L=6mm | 2
23 | M3 nut | 2

# 6 Tips and tricks

Correct operation of the toolboards and basically any 3D printer electronics depends on the environment they are used in. Even if these toolboards have lots of protection circuits, it does not mean that improper installation or usage cannot cause damage or malfunction.

Below is a list of recommendations when wiring DIY 3D printers:

1. The printer frame must be connected to mains earth and GND.
2. Aluminum bed shall be connected to frame and GND. A severe crash of the toolhead into the bed or print piece causing the toolhead to break may cause short circuits between the bed and any input or output of the toolboard (like heater, fan outputs end-stop, temperature sensor inputs, etc.). If the bed is not connected to GND, then it can have any voltage potential level, even in the range where the toolboard protection circuit is not effective anymore, leading to loss of functions or total damage.
3. Toolhead made with metal parts shall be connected to GND with extra wire using proper electrical connection washer (a washer with ribs or teeth, and hole for wire soldering). Not grounded toolheads will build up static charge, eventually, this will arc over the toolhead, which may cause electrical damage to the toolboard (less likely) or disturb communication between the toolboard and RPI causing disconnection errors (very likely scenario).
4. When connecting wires to printer frame or any aluminum parts, special washers with toots or ribs shall be used! Aluminum oxide is very good electrical insulator, therefore, using only a flat washer connector will not ensure proper electrical contact.
5. USB cables are not the best choice to supply the RPI due to high voltage drop over them. The best is to supply the RPI with 5V via the GPIO pin header pins with a proper cable. This ensures the supply voltage of the RPI is stable during sudden current load increases. Remember that when the adapter board is connected to the RPI, the supply voltage of the USB protection circuit is taken from the RPI, any disturbance in that is a potential communication disturber.

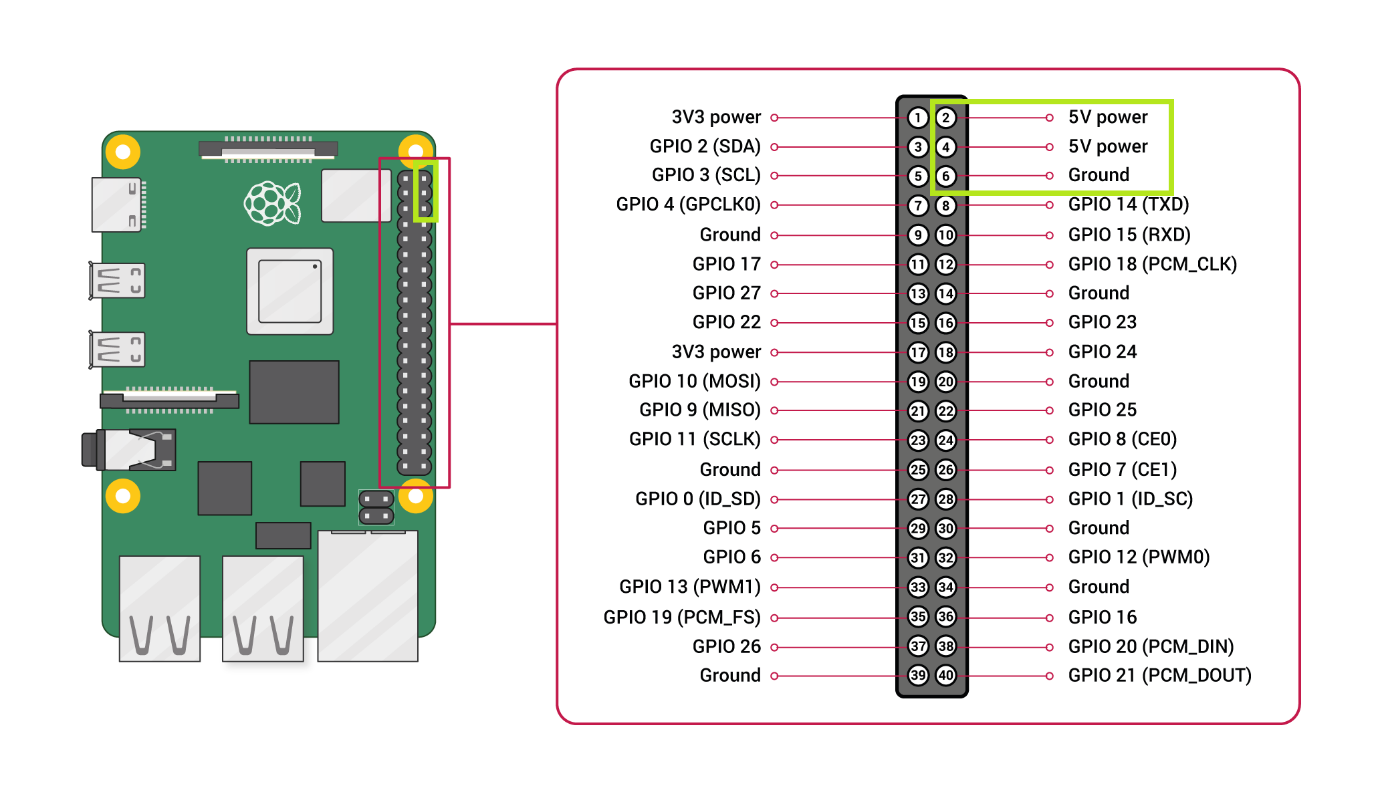
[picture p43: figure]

# 7 Electrical characteristics

# 7.1 Absolute maximum ratings

Important Note: The Orbitool O2S board can withstand these limits without electrical damage; however, long-term exposure to these limits is not recommended. The absolute maximum rating is not the same as the functional range.

The maximum ratings may not be exceeded under any circumstances!

Table 1. Orbitool O2S absolute maximum ratings

Nr. | Parameter | Min | Max | Unit
A1 | Ambient temperature range | -20 | 85 | °C
A2 | Supply voltage | -30 | 30 | V
A3 | Extruder stepper current | | 1 | A
A4 | Hot-end heater current | | 6.8 | A
A5 | Part fan output current | | 3 | A
A6 | Hot-end Fan | | 1 | A
A7 | RGB LED 5V supply current | | 0.5 | A
A8 | RGB data line output | -1 | 7 | V
A9 | USB Data lines | -1 | 28* | V
A10 | Hot-end temperature sensor input | -1 | 28* | V
A11 | End stop sensor input | -1 | 28* | V
A12 | I2C interface | -1 | 28* | V
A13 | Orbiter v2 sensor interface inputs | -1 | 3.3 | V
A14 | ESD-Protection level for handling (Human Body Model, HMB) | -8 | 8 | kV
*Should not exceed the supply voltage

# 7.2Full functional operational limits

Table 2. Orbitool O2S electrical characteristics

Nr. | Parameter | Symbol | Min | Typ | Max | Unit
| General
P1 | Operating temperature range | to | -20 | 65 | °C
P2 | Max ambient temperature with active cooling | to_cooled | | 80 | °C
P3 | Power supply voltage | vPWR | 22 | 28 | V
| Extruder stepper
P5 | Extruder stepper current (max 60°C chamber temp) | iMOT_60 | | 0.85* | A
P6 | Extruder stepper current (max 80°C chamber temp) | iMOT_80 | 0.5 | 0.6 | A
| Hot-end heater
P7 | Hot-end heater nominal current | iHEATER | | | 5 | A
P8 | Hot-end heater overcurrent switch OFF threshold | iOV_HOT | 5.9 | 6.8 | 7.2 | A
P9 | Hot-end overcurrent detection time | tOV_HOT | | | 10 | ms
P10 | Hot-end power measurement accuracy | aP_HOT | -6 | | 6 | %
| Part Fan
P11 | Part fan output current | iPART_FAN | | | 2 | A
P12 | Part fan overcurrent switch OFF threshold | iOC_PART | 4.2 | 5 | 5.8 | A
P13 | Part fan PWM frequency | fPART_FAN | 10 | | 20 | KHz
| Hot-end Cooling fan
P15 | Hot-end fan output current | iHOT_FAN | | | 0.5 | A
P16 | Hot-end fan current limitation | iCL_HOT_FAN | 2 | 3 | 3.9 | A
P17 | Hot-end fan PWM frequency | fHOT_FAN | 10 | | 20 | KHz
| External 5V supply
P18 | RGB LED + External USB current | i5V_Prot | 0.5 | A
| Internal supplies
P19 | Internal 5V supply protection current limitation | iSC_5V | 2 | 3 | 3.9 | A
P20 | Internal 3.3V supply protection current limitation | iSC_3V3 | 220 | 350 | 550 | mA
P21 | Weight | 18 | g
*Parameter derating with ambient temperature

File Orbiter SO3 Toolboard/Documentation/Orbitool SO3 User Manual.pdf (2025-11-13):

# Orbitool SO3 v1.4

Should a tool-board magic smoke come out
because of user error? Why?

Should a tool-board be destroyed by a fault in your 3D printer? Why?

My answer is NO! And this is what this toolboard is all about!

We are hobbyist and professionals, and let’s face it, we make mistakes, and when the magic smoke shows up, everybody is disappointed, even if we know it’s a user’s fault. In this board, I promise you the magic smoke is kept inside extremely tight!

Smokeless Features

- Optimized for Smart Orbiter v3 shape and features
- STM32F042 microcontroller running at 48MHz
- Automotive USB communication with a Raspberry PI
- Onboard LIS2DW12 accelerometer
- TMC2209 extruder stepper driver
- Direct connection to SO3 integrated board
- 1x PWM controlled part fan outputs
- DC-DC converter based Hot-end fan driver, compatible with 12/24V fan types with RPM speed input signal
- Hot-end temperature sensor input compatible with standard NTC or PT1000 temperature sensor types
- I/O for bed level sensor
- X-Stop sensor input
- Onboard temperature sensor
- Advanced thermal management

Protection Features

- Active short circuit protected Hot-end output
- Active short circuit protected fan driver outputs
- Active Protection circuit against reverse power supply connection
- Protection against loss of GND supply
- Analog and digital inputs protected against short to +24V supply voltage
- USB data lines are protected against short circuits to GND and +24V
- EMI interference and ESD protection on all inputs and outputs
- Heater thermal runaway protection in case of a short between heater and sense thermistor wires

Author: Dr. Róbert Lőrincz

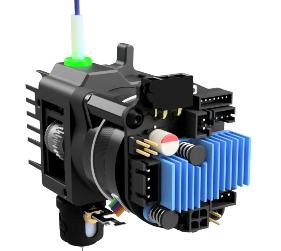
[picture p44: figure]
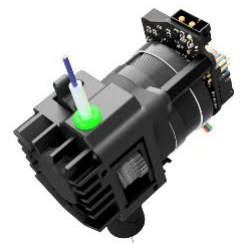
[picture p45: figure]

# 1 Block Diagram

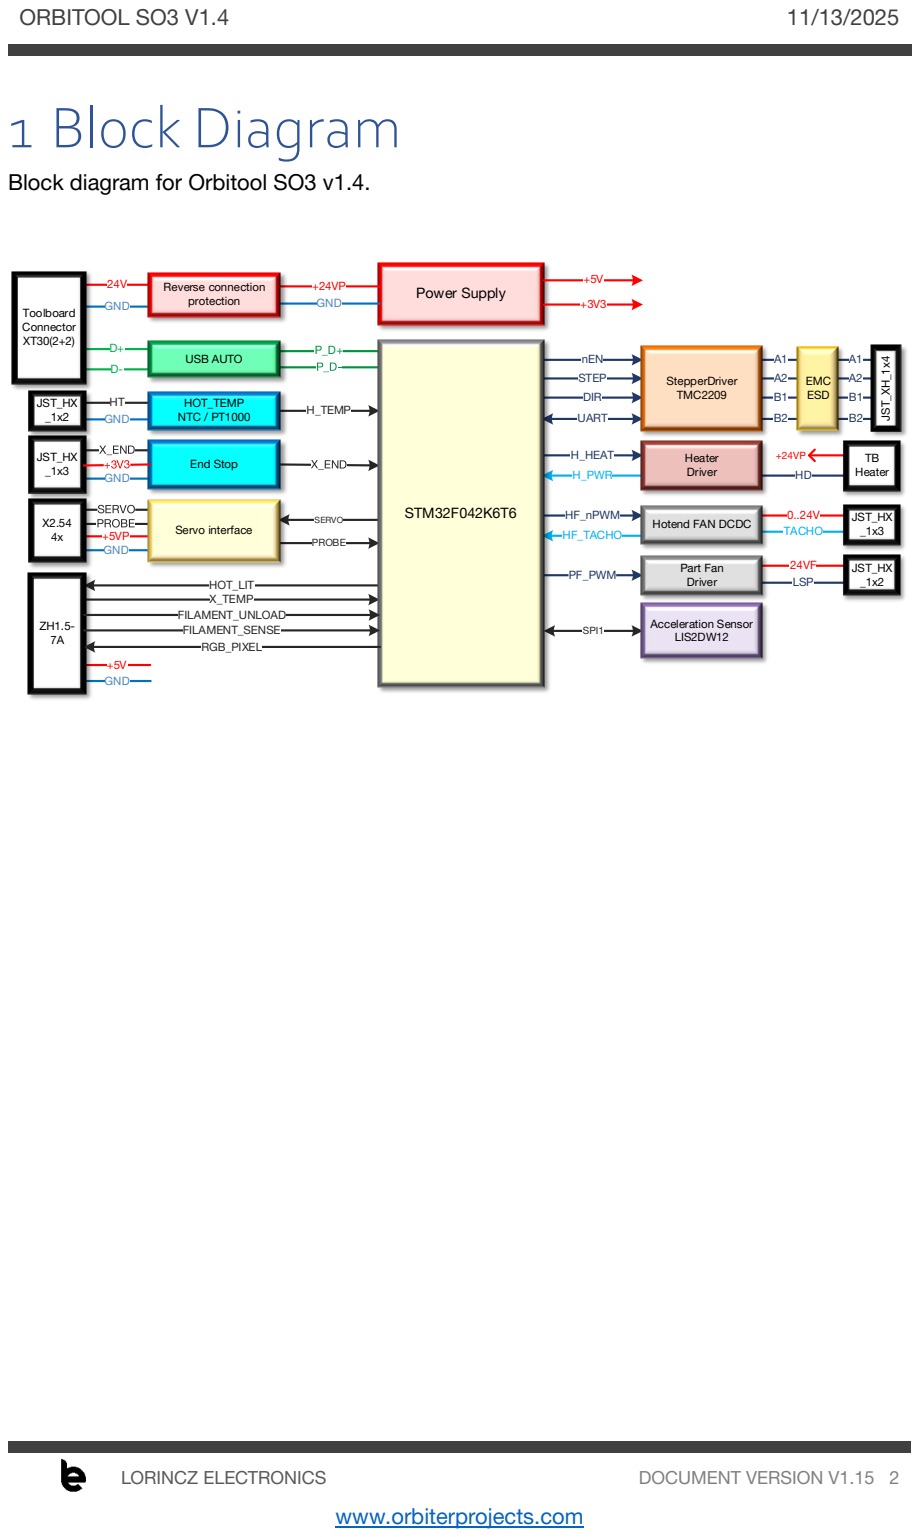
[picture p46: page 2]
ORBITOOL SO3 V1.4; LORINCZ ELECTRONICS; DOCUMENT VERSION V1.15 2; Power Supply; nEN; STEP; DIR; UART; JST_XH_1x4; EMC ESD; H_HEAT; H_PWR; Heater; Heater Driver; StepperDriver TMC2209; HF_nPWM; HF_TACHO; 0..24V TACHO; PF_PWM; LSP; JST_HX _1x3; JST_HX _1x2; Part Fan Driver; GND; HT GND; H_TEMP; HOT_LIT X_TEMP; SERVO; PROBE GND; SPI1; Toolboard Connector XT30(2+2); STM32F042K6T6; Servo interface; End Stop; HOT_TEMP NTC / PT1000; USB AUTO; Acceleration Sensor LIS2DW12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

Block diagram for Orbitool SO3 v1.4.

Hotend FAN DCDC

www.orbiterprojects.com

# 2 Pinout definition

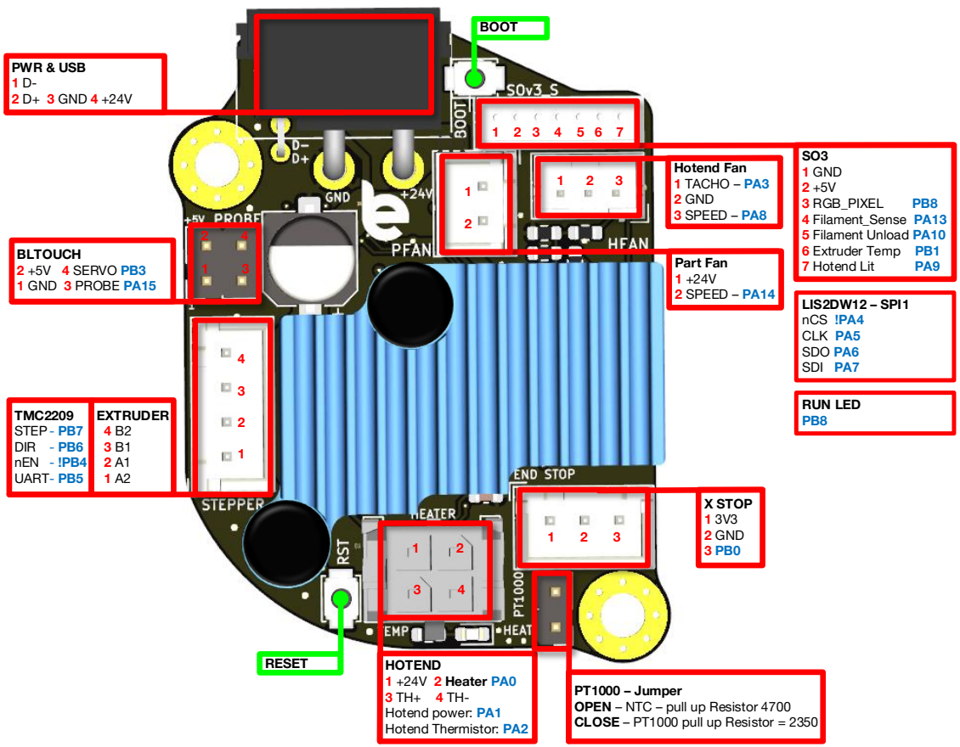
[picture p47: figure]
X STOP 1 3V3 2 GND 3 PB0; BLTOUCH 2 +5V 4 SERVO PB3 1 GND 3 PROBE PA15; HOTEND 1 +24V 2 Heater PA0 3 TH+ 4 TH- Hotend power: PA1 Hotend Thermistor: PA2; BOOT; RESET; PT1000 – Jumper OPEN – NTC – pull up Resistor 4700 CLOSE – PT1000 pull up Resistor = 2350; Hotend Fan 1 TACHO – PA3 2 GND 3 SPEED – PA8; Part Fan 1 +24V 2 SPEED – PA14; SO3 1 GND 2 +5V; 3 RGB_PIXEL; 4 Filament_Sense PA13 5 Filament Unload PA10 6 Extruder Temp PB1; 7 Hotend Lit; PWR & USB 1 D- 2 D+ 3 GND 4 +24V; LIS2DW12 – SPI1 nCS !PA4 CLK PA5 SDO PA6 SDI PA7; RUN LED PB8

TMC2209 STEP - PB7 DIR - PB6 nEN - !PB4 UART - PB5 | EXTRUDER 4 B2 3 B1 2 A1 1 A2

# 3 Features description

# 3.1 Introduction

For me, the electrical robustness of a design is part of the requirements. One of my main design goals was to integrate protection against common user errors and 3D printer defects.

In the end, nothing is more frustrating than powering up your new board and letting the magic smoke out. Even if it is due to user fault, the disappointment will still be present.

This design is based on automotive technology, where protection from all kinds of hazards is a state-of-the-art a long time ago.

This document describes the main specific features of the tool-board.

# 3.2Power supply concept

The board is supplied via an XT30 (2+2) connector, which includes +24V, GND, USB_DATA+ and USB_DATA- signals.

From the connector, the board is supplied via a reverse power supply protection circuit. This prevents tool-board damage. In the event of an accidental reversed supply by user error, the board will not start up and will behave like it’s not powered

The microcontroller is supplied from a 3.3V LDO supplied from the onboard 5V DC-DC buck converter for the highest power supply efficiency and lowest possible power consumption

# 3.3USB communication interface

The tool-board is equipped with an automotive grade USB interface. The main difference is the higher electrical robustness of the automotive USB, still maintaining highest possible communication speed. Therefore, if the USB data lines are short-to-GND or up to +28V, it will not cause any destruction and will work properly after the short circuit is removed.

The same circuit offers protection in case of GND connection loss, which will lead to biasing all the communication signals to the supply positive line (in our case, +24V).

The USB interface of the Raspberry Pi is not robust against these electrical hazards that may occur in a 3D printer. Therefore, the tool-board shall be supplied and connected to the Raspberry Pi using the supplied adapter board, which has onboard protection circuits to protect the Raspberry Pi USB port.

The next picture presents the tool-board wiring connection principle.

SO3 tool-board wiring diagram.

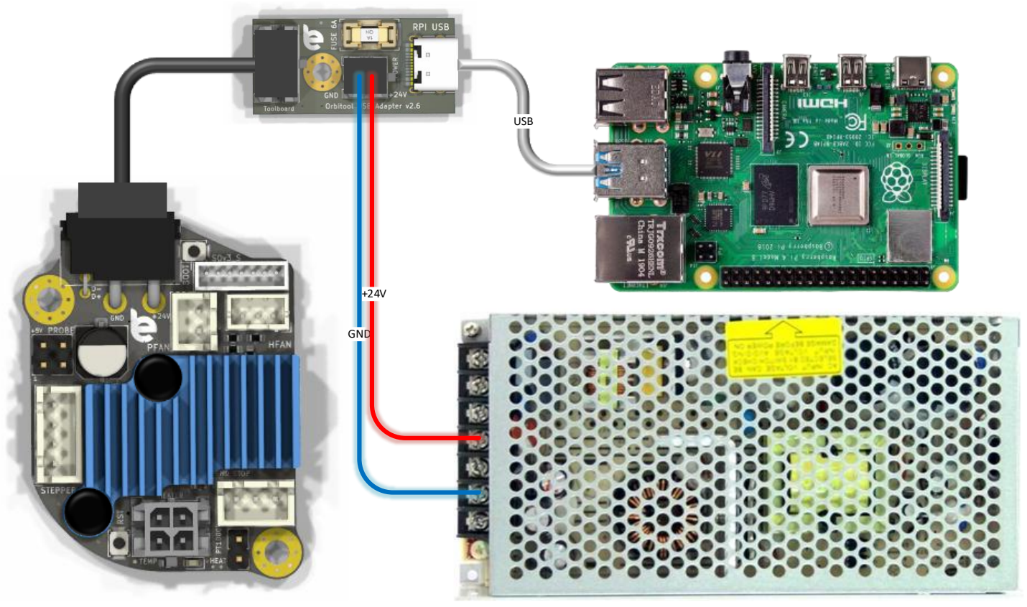
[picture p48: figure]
GND; USB

# 3.4Hot-end & temperature sensor

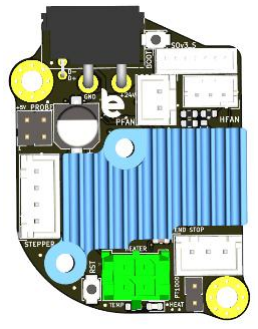
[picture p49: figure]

The hot-end temperature input circuit accepts two
types of thermal sensor elements,
- 100k NTC - ATC Semitec 104GT-2, included in the SO# hotend. Pull up resistor value 4700
- PT1000 selectable via closing Jumper PT1000. Pull up resistor value 2350. Option for connecting custom hot ends to the SO3

The senor input is protected against short circuits to GND and to the 24V supply voltage.

The SO3 tool-board has a protection circuit against dangerous thermal runaway due to a short circuit between the hotend GND and the thermistor GND connection. Without this protection the hotend heater would turn on with 100% power and go into a dangerous thermal runaway, which of course represents a fire hazard condition, and Klipper can do nothing against it. The probability of this failure, of course, is small, but considering the severity of the outcome, this board is the first to implement a protection against this event.

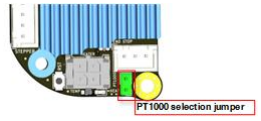
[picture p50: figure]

Hotend heater driver circuit

The hot-end heater driver circuit is implemented with active protection against short circuits.

The circuit measures the heater current and in case the current rises over a predefined threshold iOC_HOT, it switches off the heater MOSFET until the next PWM cycle to prevent damage.

The heater max power shall be limited to 99.5%, meaning max_power: 0.995 to avoid driver stuck in protection mode due to an unlikely event of a fake error detection.

The heater current is fed to Klipper, which can calculate the actual power consumption of the heater element. This can be used to detect failures of the heater element, like a short circuit or a loss of heating power.

You may say yes; other boards also have protection with onboard fuses. Well, that is simply not enough to protect MOSFETs from being damaged because fuses have a long reaction time, about 1-2s range. Their mission is to protect the circuit from catching fire in case of a defect, but it cannot protect the heater driver MOSFET from getting destroyed. This active protection reacts within 10ms, ensuring the driver stage is switched off before it gets damaged due to a short circuit or overload event.

To display the actual power of the heater, include the following section:

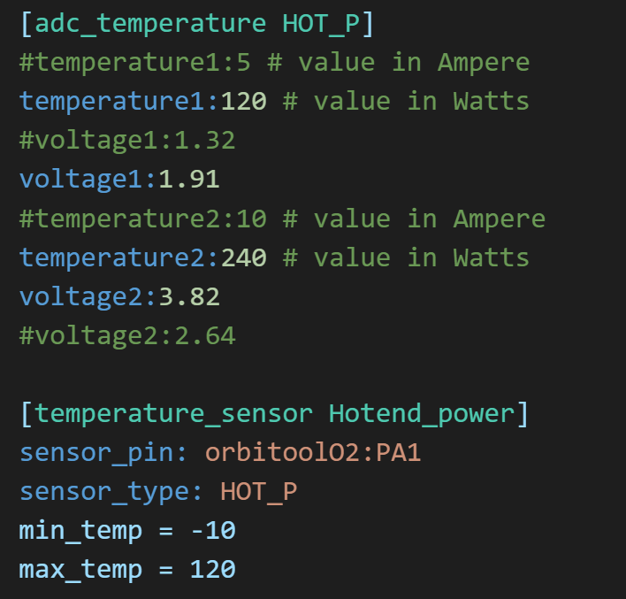
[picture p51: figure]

The hot-end power or current can be displayed based on preference. The power is calculated considering a 24V power supply.

To improve the heater power calculation accuracy, the heater PWM is forced to 100Hz (instead of the 10Hz default of Klipper).

# 3.5Fan driver outputs

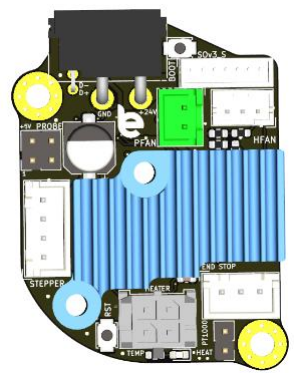
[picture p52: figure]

The fan drivers (part fan and aux / tool-board fan) have a similar protection circuit to the hot-end driver; in case of overcurrent, the fan driver is switched off until the next PWM cycle.

The PWM duty cycle of the fan driver shall be limited to 99.5%, meaning max_power: 0.995, to avoid the fan driver being stuck off due to an unlikely event of a fake error detection.

Suggested configuration of the part fan driver:

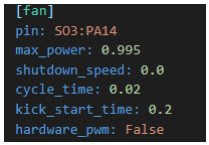
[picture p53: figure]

# 3.6Hot-end fan output

The hot-end fan circuit is implemented using a microcontroller-controlled DC-DC converter.

PWM control of three wire fans will destroy the speed signal. PWM (Pulse Width Modulation) control means switching on and off the fan power supply several times every second. This means there are moments when the fan is actually not supplied with power. In those moments, the speed sensing electronic circuit is not supplied, therefore it cannot generate a reliable speed signal. Practically, the PWM signal will be superimposed over the speed signal.

Another advantage of this control circuit is the possibility of limiting the maximum voltage according to the fan type the user has.

This output supports 12V or 24V fan types
configured by the max power value in the fan
configuration section:

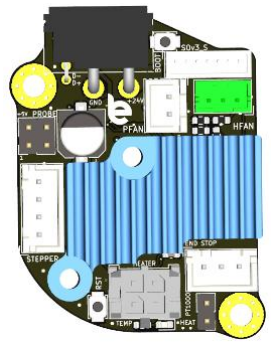
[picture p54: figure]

This output supports 12V or 24V fan types configured by the max power value in the fan configuration section:

- 12V fan – max_power: 0.5
- 24V fan – max_power: 1.0

The Smart Orbiter is equipped with a 24V fan type, so the default should be max_power :1.0.

To reduce hotend fan noise, its power can be reduced to 60%. In the case of clogs while printing very slowly, the fan speed needs to be increased.

Configuration of the Hotend fan driver:

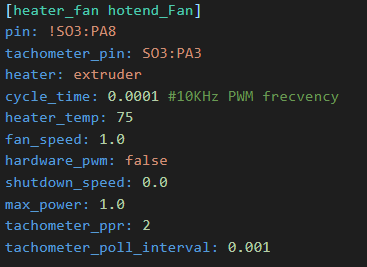
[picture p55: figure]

* Note the PWM control frequency of the circuit must be set to 10KHz, cycle time: 0.0001

Since the fan driver is based on a DC-DC converter, the PWM frequency required for correct operation is defined by the converter design, not by fan properties. Fan PWM speed control frequency shall be set to 10 Khz, cycle time = 0.0001 – do not change this to a lower frequency.

# 3.7 SO3 Extruder smart features connector

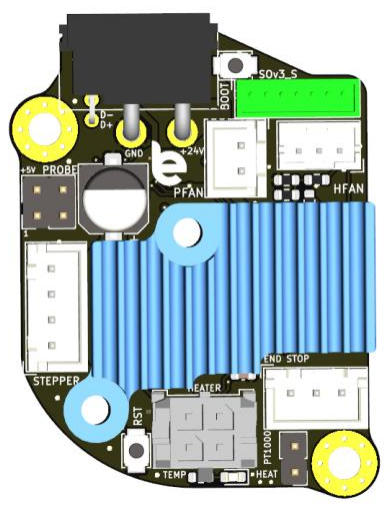
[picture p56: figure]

SO3 tool-board features a connection to the Smart Orbiter v3
internal electronics, fully supporting its features:
- Filament sensing and autoload
- Filament autounload
- RGB LED-lit filament input
- White LED hotend lit
- Extruder temperature sensor

# 3.8Thermal considerations

Closed printer chamber requires tool-board operation in high ambient temperature conditions. In addition, this tool-board is mounted on the backside of the stepper motor, which transfers a considerable amount of heat. Therefore, the circuits of this tool-board are designed to have low temperature drift and efficient thermal management to make sure none of the components heat up over their maximum allowed operation temperature.

I performed lots of thermal simulations using finite element simulations and real-life measurements using a Flir thermal camera (simulation results from the Orbiter 2 SO2 toolboard but the basic design is the same with the SO3).

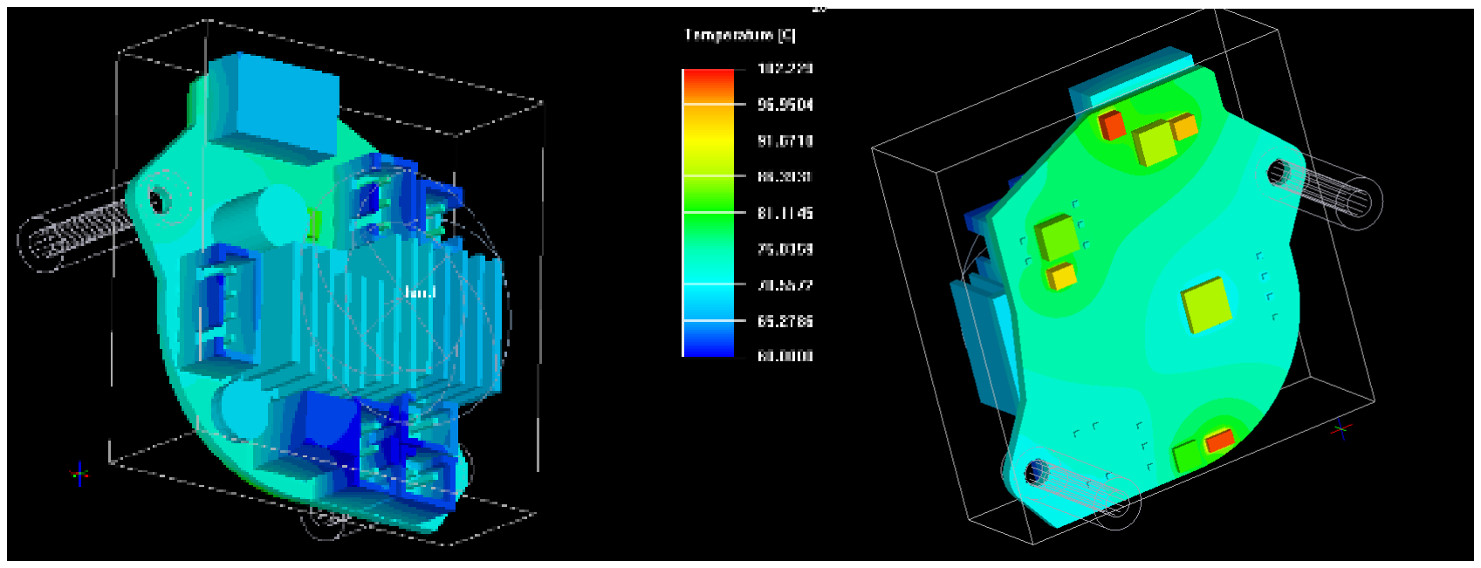
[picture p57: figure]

The simulation result show that in a 60°C chamber temperature environment, the tool-board components do not heat over their maximum junction temperature rating.

The SO3 tool-board is safe to operate in maximum 60°C ambient (printer chamber) conditions.

To reduce heat transfer from the stepper towards the tool-board a minimum distance of 4-5 mm shall be maintained. This is ensured by using the supplied standoffs.

The toolboard is designed for passive cooling, but even with the most optimized thermal design, stepper current derating over temperature still applies. This is mainly because there is simply not enough space for a bigger heatsink. Even if the heatsink size were doubled, it would still not be enough.

However, it is possible to use the SO3 tool-board in closed chamber temperatures over 60°C up to 75°C with additional measures:

- Reduce stepper current from 0.85A to 0.55A
- Use active cooling by adding a small 20x20mm or 25x25mm fan to the back of the tool-board which blows a small amount of air toward the SO3 tool-board heatsink. The power supply lines of the fan can be connected in parallel with the hotend fan.

# 4 Microcontroller programming

### 1. Connect the board to the host Raspberry Pi via a USB

adapter cable.

### 2. This step depends on whether your board has firmware

on it or not:
a) If your board is pre-flashed with Klipper, first must enter DFU mode as follows:
- press the BOOT and RESET buttons,
- release the RESET while keeping the BOOT button pressed,
- release the BOOT button after about three
seconds.
- The buttons might be a little tricky to access.

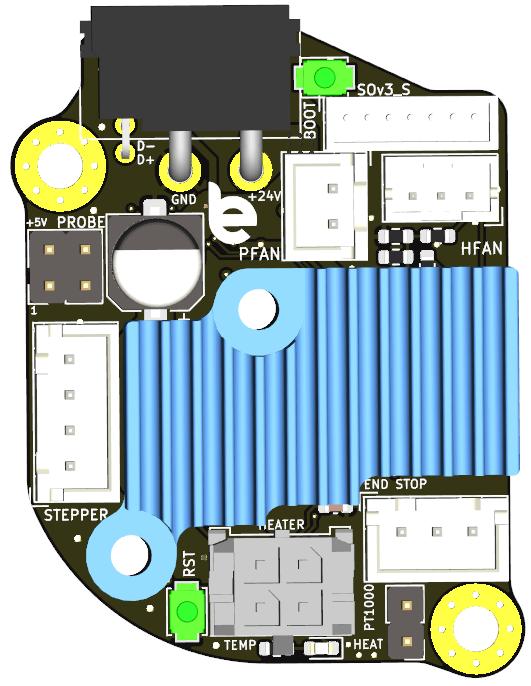
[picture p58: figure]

Hint, use some ceramic screwdriver or simple toothpicks to push the buttons and avoid creating any short over the board with metal tools
b) If your board is a new, un-flashed board:
- The MCU is already in DFU mode; confirm this at step 4

### 3. Connect to your host raspberry pi via SSH 4. Run lsusb from the command prompt

- Make sure you see an STM32 in DFU mode listed

### 5. Run dfu-util --list from the command prompt

- note the text inside the [xxxx:yyyy] (default is -> 0483:df11)

### 6. Run cd ~/klipper from the command line to enter the Klipper directory 7. Run make menuconfig settings should be:

- Cristal oscillator – 8Mhz

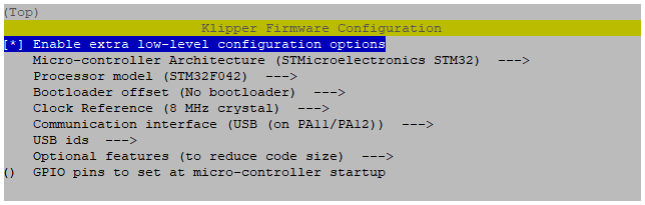
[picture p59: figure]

- Set custom USB ID to SO3Tool
- Optional features (to reduce code size):
- Hit Q to Exit and Save

### 8. Run make clean to clean up the make environment 9. Run make flash FLASH_DEVICE=0483:df11 10. In case you encounter some errors but still having the message of File downloaded

successfully than you are good to proceed to the next step.

### 11. Press the RESET button to restart the MCU and enter normal operating mode 12. Run ls /dev/serial/by-id/* should return a device beginning with:

/dev/serial/by-id/usb-Klipper_stm32f042x6_SO3Tool-if00

### 13. Copy this virtual serial port name to the SO3.cfg config file MCU section

Manual definition of USB ID, flashing the MCU with Klipper will always result in the same serial ID.

Your tool-board should now be usable with Klipper. Use the example config file to get started. The best option is to copy the config file into the same directory as printer.cfg.
Add [include SO3.cfg] to the beginning of your printer.cfg to include the file.

# 5 Assembly instructions

Based on the user setup, we can have several assembly combinations, as described below. As a recommendation, some kind of bracket with strain release for the USB cable is a must. Fixing the cable is necessary to prevent constant bending forces over the PCB during printhead movements. Even if the forces are not very high, it still stresses the PCB, and it could develop component or solder cracks. A well-designed strain release will avoid this issue.
Mount the two M3 L=18mm standoffs to the Orbiter v2 stepper’s backside.

Print the braket and the wire lock (downloadable from GitHub). (https://github.com/RobertLorincz/Orbiter-Toolboards/tree/a736aa103e1d94a642765b073b600f9c7095456a/Orbiter%20SO3%20Toolboard/3D%20CAD)

Insert the toolboard into the bracket, and using the two M3 L=8 mm and two washers fix it to the two standoffs.

Insert the USB cable and fix it into place using the
printed wire lock.


To fix the small USB adapter board to the printer frame, you may use my simple mount, as shown in the next picture. All you need is to print the mount, an M3 heat insert (L = 4~5 mm), and an M3 screw (L = 6 mm). The PCB mount can be fixed to the printer frame using two M3 screws and nuts, or attach it simply using strong foam tape.


Tool-board pack list

Orbiter v2 Toolboard pack list
Item | Description | Nr pieces / length | Type | LCSC
1 | Orbitool v1.4 | 1 | v2.72
2 | USB adapter board v2.6 | 1 | v2.6
3 | 24V USB cable | 150cm
4 | 24V power supply cable | 50cm
5 | Short USB A to USB C cable | 30cm
6 | 1 pin Dupont female connector housing | 4
7 | Dupont connector pins | 6 | A2541-TB | C339354
8 | XH-2 pin connector housing | 1 | XH-2 | C144401
9 | XH-3 pin connector housing | 1 | XH-3 | C144402
10 | XH crimp pins | 10 | SXH-001T-P0.6N | C385122
11 | M3 threaded aluminum spacer L=20mm | 2 | M3 L20
12 | M3 screw L = 8mm | 2 | M3x8
13 | Me screw L = 25 | 2 | M3x25
14 | M3 washers | 2 | M3
15 | 2.54mm Jumper | 2

# 6 Tips and tricks

Correct operation of the toolboards and basically any 3D printer electronics depends on the environment they are used. Even if these toolboards have lots of protection circuits, it does not mean that improper installation or usage cannot cause damage or malfunction.

Below is a list of recommendations when wiring DIY 3D printers:

1. The printer frame must be connected to mains earth and GND.
2. Aluminum bed shall be connected to frame and GND. A severe crash of the toolhead into the bed or print piece causing the toolhead to brake may cause short circuits between the bed and any input or output of the toolboard (like heater, fan outputs or end-stop, temperature sensor inputs, etc.). If the bed is not connected to GND, then it can have any voltage potential level even in the range where the toolboard protection circuit is not effective anymore, leading to loss of functions or total damage.
3. Toolhead made with metal parts shall be connected to GND with extra wire using proper electrical connection washer (washer with ribs or teeth, and hole for wire soldering). Not grounded toolheads will build up static charge, eventually, this will arc over the toolhead which may cause electrical damage to the toolboard (less likely) or disturb communication between the toolboard and RPI causing disconnection errors (very likely scenario).
4. When connecting wires to printer frame or any aluminum parts, special washers with toots or ribs shall be used! Aluminum oxide is very good electrical insulator, therefore using only a flat washer connector will not ensure proper electrical contact.


5. The small adapter board must be supplied with 5V, not less! The adapter board version v2.xx is taking the 5V supply from the USB-C connector. This voltage is used to supply the onboard USB protection circuit. If this voltage is less than 5V, the protection circuit may disturb the USB communication, causing toolboard disconnection failures. Note that using an improper power supply for the RPI (especially RPI 3 & 4) will lead to a lower USB voltage than 5V. The original power supplies of these PRI boards are actually providing 5.5V to compensate for the voltage loss over the internal voltage regulator and protection circuits of the RPI.

6. USB cables are not the best choice to supply the RPI due to high drop voltage over them. The best is to supply the RPI with 5V via the GPIO pin header pins with a proper cable. This ensures the supply voltage of the RPI is stable during sudden current load increases. Remember that when the adapter board is connected to the RPI, the supply voltage of the USB protection circuit is taken from the RPI, any disturbance in that is a potential communication disturber.


# 7 Electrical characteristics

# 7.1 Absolute maximum ratings

Important Note: The Orbitool SO3 board can withstand these limits without electrical damage; however, long-term exposure to these limits is not recommended. The absolute maximum rating is not the same as the functional range.

The maximum ratings may not be exceeded under any circumstances!

Table 1 Orbitool SO3 absolute maximum ratings

Nr. | Parameter | Min | Max | Unit
A1 | Ambient temperature range | -20 | 85 | °C
A2 | Supply voltage | -30 | 30 | V
A3 | Extruder stepper current | | 1 | A
A4 | Hot-end heater current | | 6.8 | A
A5 | Part fan output current | | 1 | A
A6 | Hot-end Fan | | 0.5 | A
A7 | USB Data lines | -1 | 28* | V
A8 | Hot-end temperature sensor input | -1 | 28* | V
A9 | End stop input | -1 | 28* | V
A10 | Z sensor I/O interface | -1 | +15 | V
A11 | ESD-Protection level for handling (Human Body Model, HMB) | -8 | 8 | kV
*Should not exceed the power supply voltage

# 7.2Full Operational limits

Table 2 Orbitool SO3 electrical characteristics

Nr. | Parameter | Symbol | Min | Typ | Max | Unit
| General
P1 | Operating temperature range | to | -20 | 60 | °C
P2 | Max ambient temperature with active cooling | to_cooled | | 80 | °C
P3 | Power supply voltage | vPWR | 20 | 28 | V
P4 | Power supply voltage measurement accuracy | aPWR | -3 | 3 | %
| Extruder stepper
P5 | Extruder stepper current (max 60°C chamber temp) | iMOT_60 | | 0.85* | A
P6 | Extruder stepper current (max 80°C chamber temp) | iMOT_80 | 0.5 | 0.6 | A
| Hot-end heater
P7 | Hot-end heater nominal current | iHEATER | | | 5 | A
P8 | Hot-end heater overcurrent switch OFF threshold | iOV_HOT | 5.9 | 6.8 | 7.2 | A
P9 | Hot-end overcurrent detection time | tOV_HOT | | | 10 | ms
P10 | Hot-end power measurement accuracy | aP_HOT | -6 | | 6 | %
| Part Fan
P11 | Part fan output nominal current | iPART_FAN | | | 1 | A
P12 | Part fan overcurrent switch OFF threshold | iOC_PART | 1.2 | 2 | 2.5 | A
P13 | Part fan overcurrent detection time | tOC_PART | | | 5 | ms
P15 | Part fan PWM frequency | fPART_FAN | | 100 | | Hz
| Hot-end Cooling fan
P16 | Hot-end fan output nominal current | iHOT_FAN | | | 0.4 | A
P17 | Hot-end fan current limitation | iCL_HOT_FAN | 2 | 3 | 3.9 | A
P18 | Hot-end fan PWM frequency | fHOT_FAN | 9 | 10 | 20 | Khz
| Internal supplies
P19 | Internal 5V supply protection current limitation | iSC_5V | 2 | 3 | 3.9 | A
P20 | Internal 3.3V supply protection current limitation | iSC_3V3 | 220 | 350 | 550 | mA
P21 | Weight | 18 | g
*Parameter derating with ambient temperature

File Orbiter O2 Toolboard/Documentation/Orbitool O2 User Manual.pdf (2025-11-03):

# Orbitool O2 v2.72

Should a tool-board magic smoke come out
because of user error? Why?

Should a tool-board be destroyed by a fault in your 3D printer? Why?

My answer is NO! And this is what this toolboard is all about!

We are hobbyist and professionals, and let’s face it, we make mistakes, and when the magic smoke shows up, everybody is disappointed, even if we know it’s a user’s fault. In this board, I promise you the magic smoke is kept inside extremely tight!

Smokeless Features

- Optimized for Orbiter v2 shape and features
- STM32F042 microcontroller running at 48MHz
- Automotive USB communication with a Raspberry Pi
- Onboard LIS2DW12 accelerometer
- TMC2209 extruder stepper driver
- Direct connection to the Orbiter v2 sensor
- 2x PWM controlled fan outputs
- DC-DC converter based hot-end fan driver, compatible with 12/24V fan types with RPM speed input signal
- Hot-end temperature sensor input compatible with standard NTC or PT1000 temperature sensor types
- I/O for bed level sensing
- X-Stop sensor input
- RGB LED driver output
- Onboard temperature sensor
- Advanced thermal management

Protection Features

- Active short circuit protected Hot-end output
- Active short circuit protected fan driver outputs
- Active Protection circuit against reverse power supply connection
- Protection against loss of GND supply
- Analog and digital inputs protected against short to +24V supply voltage
- USB data lines are protected against short circuits to GND and +24V
- RGB LED power supply pin protected against short to GND
- EMI interference and ESD protection for all inputs and outputs
- Heater thermal runaway protection in case of a short between heater and sense thermistor wires

Author: Dr. Róbert Lőrincz


# 1 Block Diagram

Power Supply; nEN; STEP; DIR; UART; JST_XH_1x4; EMC ESD; H_HEAT; H_PWR; Heater; Heater Driver; StepperDriver TMC2209; RGB; +5VP RGB; HF_nPWM; HF_TACHO; TACHO; PF_PWM; TF_PWM; 24VF LST; LSP; JST_XH _1x3; JST_XH _1x2; Part Fan Driver; Toolboard FanDriver; GND; X_END; H_TEMP; F_UNLOAD; SERVO; PROBE GND; SPI1; Toolboard Connector XT30(2+2); JST_XH_1 x2; STM32F042K6T6/7; Servo interface; Filament Sensor & Unload; End Stop; HOT_TEMP NTC / PT1000; USB AUTO; Acceleration Sensor LIS2DW12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

Block diagram for Orbitool 02 v2.72

RGB LED Driver

Hotend FAN DCDC

ORBITOOL O2 V2.72 | 11/03/2025

Part FAN 1 +24V 2 PA10; HOT FAN 3 SPEED !PA9 2 GND 1 Tacho PA8; EXTRUDER 4 B2 3 B1 2 A1 1 A2; TMC2209 STEP DIR nEN UART; BLTOUCH 1 GND 2 +5V 3 PROBE PA15 4 GND 5 SERVO PB3; HOT TEMP 1 PA3 2 GND; X STOP 1 PB0 2 GND; RGB 1 +5V 2 PA1 3 GND; HOTEND 1 +24V 2 PA0 POWER PA2; Orbiter v2 Sensor 4 FIL_UNLOAD PA14 3 FIL_SENZ PA13 2 3.3V 1 GND; BOOT; RESET; LIS2DW12 – SPI1 nCS !PA4 CLK PA5 SDO PA6 SDI PA7; POWER & USB 1 D- 2 D+ 3 GND 4 +24V; Tool FAN 1 +24V 2 PB1; RUN LED PB8

LORINCZ ELECTRONICS | DOCUMENT VERSION V1.13 3
www.orbiterprojects.com

# 2 Pinout definition

# 3 Features description

# 3.1 Introduction

For me, the electrical robustness of a design is part of the requirements. One of my main design goals was to integrate protection against common user errors and 3D printer defects.

In the end, nothing is more frustrating than powering up your new board and letting the magic smoke out. Even if it is due to user fault, the disappointment will still be present.

This design is based on automotive technology, where protection from all kinds of hazards is a state-of-the-art a long time ago.

This document describes the main specific features of the tool-board.

# 3.2Power supply concept

The board is supplied via an XT30 (2+2) connector, which includes +24V, GND, USB_DATA+ and USB_DATA- signals.

From the connector, the board is supplied via a reverse power supply protection circuit. This prevents tool-board damage. In the event of an accidental reversed supply by user error, the board will not start up and will behave like it’s not powered.

The microcontroller is supplied from a 3.3V LDO supplied from the onboard 5V DC-DC buck converter for the highest power supply efficiency and lowest possible power consumption.

The RGB LED and the bed level sensor outputs are supplied from a short-to-GND protected power supply.

# 3.3USB communication interface

The tool-board is equipped with an automotive grade USB interface. The main difference is the higher electrical robustness of the automotive USB, still maintaining highest possible communication speed. Therefore, if the USB data lines are short-to-GND or up to +28V, it will not cause any destruction and will work properly after the short circuit is removed.

The same circuit offers protection in case of GND connection loss, which will lead to biasing all the communication signals to the supply positive line (in our case, +24V).

The USB interface of the Raspberry Pi is not robust against these electrical hazards that may occur in a 3D printer. Therefore, the tool-board shall be supplied and connected to the Raspberry Pi using the supplied adapter board, which has onboard protection circuits to protect the Raspberry Pi USB port.

The next picture presents the tool-board wiring connection principle.

GND; USB

# 3.4Hot-end temperature sensor

The hot-end input circuit accepts two types of thermistors, 100k NTC type similar to the ATC Semitec 104GT-2 and PT1000.

Pull-up resistor value: 2200Ω.

The senor input is protected against short circuits to GND and supply voltage of 24V.

The GND connection of the sensor is current limited to avoid thermal runaway of the hotend in the event of a short circuit between the sensor and heater wires.

# 3.5Driver circuit for hot-end heater

The hot-end heater driver circuit is implemented with
active protection against short circuits.

The circuit measures the heater current and in case the current rises over a predefined threshold iOC_HOT, it switches off the heater MOSFET until the next PWM cycle to prevent damage.

The heater max power shall be limited to 99.5%,
meaning | max_power: 0.995 | to avoid driver stuck in
protection mode due to an unlikely event of a fake error detection.

The heater current is fed to Klipper, which can calculate


the actual power consumption of the heater element. This can be used to detect failures of the heater element, like a short circuit or a loss of heating power.

You may say yes; other boards also have protection with onboard fuses. Well, that is simply not enough to protect MOSFETs from being damaged because fuses have a long reaction time, about 1-2s range. Their mission is to protect the circuit from catching fire in case of a defect, but it cannot protect the heater driver MOSFET from getting destroyed. This active protection reacts within 10ms, ensuring the driver stage is switched off before it gets damaged due to a short circuit or overload event.

To display the actual power of the heater, include the following section:


The hot-end power or current can be displayed based on preference. The power is calculated considering a 24V power supply.

To improve the heater power calculation accuracy, the heater PWM is forced to 100Hz (instead of the 10Hz default of Klipper).

It is highly recommended to use ferules to connect the heater wires to the tool-board screw terminal block.

# 3.6Fan driver outputs


The fan drivers (part fan and aux / tool-board fan) have a similar protection circuit to the hot-end driver; in case of overcurrent, the fan driver is switched off until the next PWM cycle.

The PWM duty cycle of the fan driver shall be limited
to 99.5%, meaning | max_power: 0.995, | to avoid the
fan driver being stuck off due to an unlikely event of a fake error detection.

Suggested configuration of the part fan driver:

# 3.7 Hot-end fan output


The hot-end fan circuit is implemented using a microcontroller-controlled DC-DC converter.

PWM control of three wire fans will destroy the speed signal. PWM (Pulse Width Modulation) control means switching on and off the fan power supply several times every second. This means there are moments when the fan is actually not supplied with power. In those moments, the speed sensing electronic circuit is not supplied, therefore it cannot generate a reliable speed signal. Practically, the PWM signal will be superimposed over the speed signal.

Another advantage of this control circuit is the possibility of limiting the maximum voltage according to the fan type the user has.

This output supports 12V or 24V fan types configured by the max power value in the fan configuration section:

- 12V fan – max_power: 0.5
- 24V fan – max_power: 1.0

Since the fan driver is based on a DC-DC converter, the PWM frequency required for correct operation is defined by the converter design, not by fan properties. Fan PWM speed control frequency shall be set to 10 Khz, cycle time = 0.0001 – do not change this to a lower frequency.

Based on a specific printer design, the maximum power can be limited to reduce fan noise. Increase this to a higher level in case you experience hot end clogs.

The connection of a three-wire fan should respect the following wiring:


Klipper configuration example:


The connection of a two-wire fan should respect the following wiring:


In the Klipper configuration, the tachometer related definitions shall be commented out as follows:


# 3.8BQ microprobe connection

The following diagram shows how to connect the BQ microprobe to the toolboard. Note that the wiring is slightly different from the standard pinout the probes come with. The white and yellow wires must be swapped in between them.

For the probe definition, do not activate the pull up in the microcontroller, use it without the ‘^” pull-up activation command!

Klipper configuration:


Important disclaimer! We have found out that with these changes some microprobes would still not work properly. Even if with other boards these probes might perform better our investigation shows the real root cause of the probe not working correctly together with our toolboard is the microprobe poor electrical and mechanical design quality. Considering all of this result we do not recommend the usage of the BQ Microprobe together with the orbiter toolboard series.

# 3.9Thermal considerations

Closed printer chamber requires tool-board operation in high ambient temperature conditions. In addition, this tool-board is mounted on the backside of the stepper motor, which transfers a considerable amount of heat. Therefore, the circuits of this tool-board are designed to have low temperature drift and efficient thermal management to make sure none of the components heat up over their maximum allowed operation temperature.

I performed lots of thermal simulations using finite element simulations and real-life measurements using a Flir thermal camera.


The simulation result show that in a 60°C chamber temperature environment, the tool-board components do not heat over their maximum junction temperature rating.

To reduce heat transfer from the stepper towards
the tool-board a minimum distance of 4-5 mm shall be maintained. Orbiter V2 equipped with the LDO-36STH20-1004AHG steper and the Orbiter sensor, standoffs of 18 mm length are recommended. This way, the distance between the toolboard PCB and the stepper back side is about 5 mm.

Without the Orbiter sensor, the standoff length shall be minimum 20 mm.

The toolboard is designed for passive cooling,
but even with the most optimized thermal
design, | stepper | current | derating | over


temperature still applies. This is mainly because there is simply not enough space for a bigger heatsink. Even if the heatsink size were doubled, it would still not be enough.

Therefore, we have two possible solutions:

1. Reduce stepper current for high ambient temperature operation. Example down to 0.55A for chamber temperature above 60°C.
2. Use active cooling to improve the thermal behavior. Adding a small 20x20mm or 25x25mm fan on the back of the toolboard that blows air toward the heatsink will
| improve a lot.

# 4 Microcontroller programming

1. Connect the board to the host Raspberry Pi via a USB adapter cable.

### 2. This step depends on whether your board has firmware on it or not:

a) If your board is pre-flashed with Klipper, first must enter DFU mode as follows:
- press the BOOT and RESET buttons,
- release the RESET while keeping the BOOT button pressed,
- release the BOOT button after about three seconds.
b) If your board is a new, un-flashed board:
- The MCU is already in DFU mode; confirm this at step 4

BOOT

RESET


### 3. Connect to your host Raspberry Pi via SSH 4. Run lsusb from the command prompt

- Make sure you see an STM32 in DFU mode listed

### 5. Run dfu-util --list from the command prompt

- note the text inside the [xxxx:yyyy] (default is -> 0483:df11)

### 6. Run cd ~/klipper from the command line to enter the Klipper directory 7. Run make menuconfig settings should be:

- Cristal oscillator – 8Mhz


- Set custom USB ID to OrbitoolO2
- Optional features (to reduce code size):
- Hit Q to Exit and Save

### 8. Run make clean to clean up the make environment 9. Run make flash FLASH_DEVICE=0483:df11

If you encounter some errors but still have the message of File downloaded successfully, you are good to proceed to the next step.

### 10. Press the RESET button to restart the MCU and enter normal operating mode 11. Run ls /dev/serial/by-id/* should return a device with

/dev/serial/by-id/usb-Klipper_stm32f042x6_OrbitoolO2-if00
Copy this virtual serial port name to the OrbitoolO2 config file in the MCU section

Manual definition of USB ID, flashing the MCU with Klipper will always result in the same serial ID.

Your tool-board should now be usable with Klipper. Use the example config file to get started. The best option is to copy the config file into the same directory as printer.cfg.
Add [include OrbitoolO2.cfg] to the beginning of your printer.cfg to include the file.
Comment out the unused I/O features of the OrbitoolO2 config section.

# 5 Assembly instructions

Based on the user setup, we can have several assembly combinations, as described below. As a recommendation, some kind of bracket with strain release for the USB cable is a must. Fixing the cable is necessary to prevent constant bending forces over the PCB during printhead movements. Even if the forces are not very high, it still stresses the PCB, and it could develop component or solder cracks. A well-designed strain release will avoid this issue.

# 5.1Orbiter v2 + Orbitool + Bracket


Mount the two M3 L=18mm standoffs to the Orbiter v2 stepper’s backside.

Print the braket and the wire lock (downloadable from GitHub). (https://github.com/RobertLorincz/Orbiter-Toolboards/tree/main/Orbiter%20O2%20Toolboard/3D%20CAD)

Insert the toolboard into the bracket, and using the two M3 L=8 mm and two washers fix it to the two standoffs.

Insert the USB cable and fix it into place using the printed wire lock.

# 5.2 Orbiter v2 + Orbitool


Change the two screws holding the Orbiter v2 together with the longer ones provided in the toolboard package (M3 L=25mm).

Add two M3 nuts over the screws on back side of the stepper, after which mount the two M3 L=18mm standoffs as shown in the picture.

Attach the toolboard and secure it in place with the M3 L=8mm screw sets and washers provided in the toolboard kit.

# 5.3Orbiter v2 + Orbitool + Orbiter sensor

Mount the Orbiter sensor over the top of the
Orbiter v2, using the two longer M3 screw sets provided in the sensor kit.

Insert the small interconnection part between the sensor and the toolboard into the sensor connector.

Screw on the two M3 standoffs with 18mm length over the sensor back side.

Attach the toolboard and secure it in place with the M3 L=8mm screw sets and washers provided in the toolboard kit.


# 5.4 Orbiter v2 + Orbitool + sensor + bracket


Mount the Orbiter sensor over the top of the Orbiter
v2, using the two longer M3 screw sets provided in the sensor kit.

Print the braket and the wire lock (downloadable from GitHub). (https://github.com/RobertLorincz/Orbiter-Toolboards/tree/main/Orbiter%20O2%20Toolboard/3D%20CAD)

Insert the small interconnection part between the sensor and the toolboard into the sensor connector.

Screw on the two M3 standoffs with 14mm length over the sensor back side.

Insert the toolboard into the bracket, and using the two M3 L=8 mm and two washers, fix it to the two standoffs.

Insert the USB cable and fix it into place using the printed wire lock.

# 5.5USB adapter board bracket

To fix the small USB adapter board to the printer frame, you may use my simple mount, as shown in the next picture. All you need is to print the mount, an M3 heat insert (L = 4~5 mm), and an M3 screw (L = 6 mm). The PCB mount can be fixed to the printer frame using two M3 screws and nuts, or attach it simply using strong foam tape.


# 5.6 Toolboard pack list

Orbiter v2 Toolboard pack list
Item | Description | Nr pieces / length | Type | LCSC
1 | Orbitool v2.72 | 1 | v2.72
2 | USB adapter board v2.6 | 1 | v2.6
3 | 24V USB cable | 150cm
4 | 24V power supply cable | 50cm
5 | Short USB A to USB C cable | 30cm
6 | Orbiter Sensor connecting bridge | 1 | | C2718488
7 | 5 pin Dupont female connector housing | 1 | A2541H-5P | C339333
8 | Dupont connector pins | 6 | A2541-TB | C339354
9 | XH-2 pin connector housing | 4 | XH-2 | C144401
10 | XH-3 pin connector housing | 2 | XH-3 | C144402
11 | XH-4 pin connector housing | 1 | XH-4 | C144403
12 | XH crimp pins | 25 | SXH-001T-P0.6N | C385122
13 | Ferules for 1mm^2 | 4 | VE1008
14 | M3 threaded aluminum spacer L=18mm | 2 | M3 L18
15 | M3 screw L = 8mm | 2 | M3x8
16 | Me screw L = 25 | 2 | M3x25
17 | M3 washers | 2 | M3
18 | M3 nut | 2 | M3

# 6 Tips and tricks

Correct operation of the toolboards and basically any 3D printer electronics depends on the environment they are used. Even if these toolboards have lots of protection circuits, it does not mean that improper installation or usage cannot cause damage or malfunction.

Below is a list of recommendations when wiring DIY 3D printers:

1. The printer frame must be connected to mains earth and GND.
2. Aluminum bed shall be connected to frame and GND. A severe crash of the toolhead into the bed or print piece causing the toolhead to brake may cause short circuits between the bed and any input or output of the toolboard (like heater, fan outputs or end-stop, temperature sensor inputs, etc.). If the bed is not connected to GND, then it can have any voltage potential level even in the range where the toolboard protection circuit is not effective anymore, leading to loss of functions or total damage.
3. Toolhead made with metal parts shall be connected to GND with extra wire using proper electrical connection washer (washer with ribs or teeth, and hole for wire soldering). Not grounded toolheads will build up static charge, eventually, this will arc over the toolhead which may cause electrical damage to the toolboard (less likely) or disturb communication between the toolboard and RPI causing disconnection errors (very likely scenario).
4. When connecting wires to printer frame or any aluminum parts, special washers with toots or ribs shall be used! Aluminum oxide is very good electrical insulator, therefore using only a flat washer connector will not ensure proper electrical contact.


5. The small adapter board must be supplied with 5V, not less! The adapter board version v2.xx is taking the 5V supply from the USB-C connector. This voltage is used to supply the onboard USB protection circuit. If this voltage is less than 5V, the protection circuit may disturb the USB communication, causing toolboard disconnection failures. Note that using an improper power supply for the RPI (especially RPI 3 & 4) will lead to a lower USB voltage than 5V. The original power supplies of these PRI boards are actually providing 5.5V to compensate for the voltage loss over the internal voltage regulator and protection circuits of the RPI.

6. USB cables are not the best choice to supply the RPI due to high drop voltage over them. The best is to supply the RPI with 5V via the GPIO pin header pins with a proper cable. This ensures the supply voltage of the RPI is stable during sudden current load increases. Remember that when the adapter board is connected to the RPI, the supply voltage of the USB protection circuit is taken from the RPI, any disturbance in that is a potential communication disturber.


# 7 Electrical characteristics

# 7.1 Absolute maximum ratings

Important Note: The Orbitool O2 board can withstand these limits without electrical damage; however, long-term exposure to these limits is not recommended. The absolute maximum rating is not the same as the functional range.

The maximum ratings may not be exceeded under any circumstances!

Table 1. Orbitool O2 absolute maximum ratings

Nr. | Parameter | Min | Max | Unit
A1 | Ambient temperature range | -20 | 85 | °C
A2 | Supply voltage | -30 | 30 | V
A3 | Extruder stepper current | | 1 | A
A4 | Hot-end heater current | | 6.8 | A
A5 | Part fan output current | | 1 | A
A6 | Hot-end Fan | | 1 | A
A7 | RGB LED 5V supply current | | 0.5 | A
A8 | RGB data line output | -1 | 7 | V
A9 | USB Data lines | -1 | 28* | V
A10 | Hot-end temperature sensor input | -1 | 28* | V
A11 | End stop sensor input | -1 | 28* | V
A12 | Z sensor I/O interface | -10 | +15 | V
A13 | Orbiter v2 sensor interface inputs | -1 | 3.3 | V
A14 | ESD-Protection level for handling (Human Body Model, HMB) | -8 | 8 | kV
*Should not exceed the supply voltage

# 7.2Full functional operational limits

Table 2. Orbitool O2 electrical characteristics

Nr. | Parameter | Symbol | Min | Typ | Max | Unit
| General
P1 | Operating temperature range | to | -20 | 60 | °C
P2 | Max ambient temperature with active cooling | to_cooled | | 80 | °C
P3 | Power supply voltage | vPWR | 22 | 28 | V
P4 | Power supply voltage measurement accuracy | aPWR | -3 | 3 | %
| Extruder stepper
P5 | Extruder stepper current (max 60°C chamber temp) | iMOT_60 | | 0.85* | A
P6 | Extruder stepper current (max 80°C chamber temp) | iMOT_80 | 0.5 | 0.6 | A
| Hot-end heater
P7 | Hot-end heater nominal current | iHEATER | | | 5 | A
P8 | Hot-end heater overcurrent switch OFF threshold | iOV_HOT | 5.9 | 6.8 | 7.2 | A
P9 | Hot-end overcurrent detection time | tOV_HOT | | | 10 | ms
P10 | Hot-end power measurement accuracy | aP_HOT | -6 | | 6 | %
| Part Fan, Tool FAN
P11 | Part fan output current | iPART_FAN | | | 1 | A
P12 | Part fan overcurrent switch OFF threshold | iOC_PART | 1.2 | 2 | 2.5 | A
P13 | Part fan overcurrent detection time | tOC_PART | | | 5 | ms
P14 | Part fan PWM frequency | fPART_FAN | | 100 | | Hz
| Hot-end Cooling fan
P15 | Hot-end fan output current | iHOT_FAN | | | 0.5 | A
P16 | Hot-end fan current limitation | iCL_HOT_FAN | 2 | 3 | 3.9 | A
P17 | Hot-end fan PWM frequency | fHOT_FAN | 9 | 10 | 20 | Khz
| External 5V supply
P18 | RGB LED + bed level sensor supply current | i5V_Prot | 0.5 | A
| Internal supplies
P19 | Internal 5V supply protection current limitation | iSC_5V | 2 | 3 | 3.9 | A
P20 | Internal 3.3V supply protection current limitation | iSC_3V3 | 220 | 350 | 550 | mA
P21 | Weight | 18 | g
*Parameter derating with ambient temperature

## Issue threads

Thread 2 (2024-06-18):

schematic?

Fisheiyy, 2024-06-18:
please post schematic for this toolhead board

RobertLorincz, 2024-07-04:
Schematic is not planned to be released at this point. This is a complete new development, not a copy of existing boards. For now we do not want to make competitors job easy. I will release it in the future, but not now.

qOtXqi, 2025-06-16:
@RobertLorincz Any news on the release of the schematics for the O2 now that the O2s is out? Thanks.

RobertLorincz, 2025-07-17:
I do not think we will release the schematics soon.

Closed 2024-07-15.

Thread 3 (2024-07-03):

Add dimensions to documentation

Norvat, 2024-07-03:
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

RobertLorincz, 2024-07-04:
I shared .step files with complete dimension, what additional info would a 2D drawing add?

Norvat, 2024-07-04:
Would just make it a bit easier for us that isn't going to use the board mounted to the orbiter to see the size and bolt pattern without opening a cad program :)

Closed 2024-07-15.

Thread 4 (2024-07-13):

No mounting option for PCB board O2 toolboard kit

Johan501, 2024-07-13:
It seems that there isnt any way to mount the USB PCB somewhere?
(printable mount like the LDO Nitehawks has)

Johan501, 2024-07-15:
I litterally can't continue my LDO Voron 2.4 rebuild for days now.... so I'm pretty frustrated to be really honest.

RobertLorincz, 2024-07-15:
The only design I've made is to attach it to the back of the stepper motor. The fixing holes are also designed in a way to fit there perfectly. This does not mean you cannot mount it anywhere else. You would just need some adapters or a way to fix it where it is better suited for you.

Johan501, 2024-07-15:
> The only design I've made is to attach it to the back of the stepper motor. The fixing holes are also designed in a way to fit there perfectly. This does not mean you cannot mount it anywhere else. You would just need some adapters or a way to fix it where it is better suited for you.

Hi, thanks for your reply, but are you talking the toolhead board itself?
I was talking about the USB PCB board, not toolhead board. That was has 2 brackets. But I digress.

RobertLorincz, 2024-07-15:
I see, I misunderstood your issue. I thought you are talking about the Toolboard. Now I see you mean the small USB adapter PCB. Give me a min and I upload the design I use on my printer.

Johan501, 2024-07-15:
Hi,

It's okay!
And thank you very much!
I saw on Twitter that someone else also had the same issue and probably
others maybe too.

Take your time, I'm already glad you will upload it! :)

Today I made one myself, not sure yet if it will work. I probably going to
use yours. But in general it's better to have it uploaded. :)

Kind regards,
Johan

Op ma 15 jul 2024 18:42 schreef LorinczElectronics ***@***.***
>:

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

RobertLorincz, 2024-07-15:
I uploaded my version together with the adapter board CAD model. I also included the Fusion 360 and .step files, so people can modify as they wish; maybe my mount will not fit everyone. I also updated the toolboard user manual.

Johan501, 2024-07-15:
Okay awesome, thank you! 😊🤘🙏

Op ma 15 jul 2024 19:16 schreef LorinczElectronics ***@***.***
>:

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

Closed 2024-07-16.

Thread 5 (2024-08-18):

toolboard mounting spacers found, my apology

jjl40, 2024-08-18:
I am assembling my orbiter V3 and don't see any spacers in the installation kit. I have looked at all the documentation and have not found a BOM for the kit. Kind of inconvenient and disappointing running into this type of problem on the weekend when you are looking forward to trying out some new equipment.
I'm not sure if the kit is supposed to include these items but I have come to expect more from LDO.

Closed 2024-08-19.

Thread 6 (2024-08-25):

SO3 tool board compatible with BIQU Microprobe?

davey242, 2024-08-25:
Is the SO3 tool board compatible with BTT BIQU Microprobe?

I have a 3D Touch (BL Touch knockoff) connect and working. I am trying to replace with the BIQU Microprobe (v2). I added the Klipper code for the BIQU but it is not triggering. It only shows open and cannot home the Z without it hitting the bed (I use my finger to text above the bed).
Probe up and down work to raise/lower

Have tried with pin: ^!SO3:PA15 and pin: !SO3:PA15 with no luck. QUERY_PROBE will always show open.

`[output_pin probe_enable]
pin: SO3:PB3  # Set to the control pin on your board
value: 0

[probe]
pin: ^!SO3:PA15 # NOTE FOR V2 users: Set this to ^!PC14 to set the low level trigger
deactivate_on_each_sample: False
x_offset: 0
y_offset: -35
z_offset: 0  # Will be overridden when you do a PROBE_CALIBRATE
samples: 2
speed: 5
samples_tolerance: 0.05
samples_tolerance_retries: 3
sample_retract_dist: 4
activate_gcode:
    PROBE_DOWN
    G4 P500
deactivate_gcode:
    PROBE_UP `

swaggy111, 2024-08-26:
Download
https://www.mediafire.com/file/ynhx37qmyqek881/fix.zip/file
In the installer menu, select "gcc."

swaggy111, 2024-08-26:
Download
https://www.dropbox.com/scl/fi/ku9a1wblqyb84rb8ekase/fix.zip?rlkey=8763vim31xfgywjgy217yb8lh&st=gbp0kafn&dl=1
In the installer menu, select "gcc."

swaggy111, 2024-08-26:
Download
https://www.dropbox.com/scl/fi/ku9a1wblqyb84rb8ekase/fix.zip?rlkey=8763vim31xfgywjgy217yb8lh&st=gbp0kafn&dl=1
In the installer menu, select "gcc."

RobertLorincz, 2024-08-28:
Hi, yes, it shall work. We discussed it with the O2 toolboard having the same issue, I updated the documentation for the O2 toolboard, connection to the O3 toolboard is similar. check the latest documentation for the O2 Toolboard. The pinout of the connectors are different but the signal names are the same. I will update the SO3 toolboard documentation soon with the microprobe.

davey242, 2024-08-29:
the BQ probe has White as Probe and Yellow as Server.
PB3 is server and PA15 is probe
Switching the White and Yellow as in the SO2 doc does not make sense as it would be wired incorrectly but the probe does not work with white on PA15 and yellow on PB2 with PA15 as !PA15 or ^!PA15.

I swapped the yellow and white as in the SO2 Documentation and as expected, the probe would not go down/up with the macros. I then swapped the pins in the config (essentially putting it back the way it was but on swapped pins) and the probe would go down/up by macro.

using just ! on PB3 did not work but it is working with ^!PB3

Final working config is below which is the same as original post except for the yellow and white wire swapped and the pins in the config swapped to match.

`[output_pin probe_enable]
pin: SO3:PA15  # Set to the control pin on your board
value: 0

[probe]
pin: ^!SO3:PB3 # NOTE FOR V2 users: Set this to ^!PC14 to set the low level trigger
deactivate_on_each_sample: False
x_offset: 0
y_offset: -35
z_offset: 0  # Will be overridden when you do a PROBE_CALIBRATE
samples: 2
speed: 5
samples_tolerance: 0.05
samples_tolerance_retries: 3
sample_retract_dist: 4
activate_gcode:
    PROBE_DOWN
    G4 P500
deactivate_gcode:
    PROBE_UP`

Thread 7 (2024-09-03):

Klipper not recognising so3 board

Naclifford, 2024-09-03:
I’ve connected the board up, I’ve connected to klipper via ssh and the board isn’t listed in the usb section or to get the board to be recognised dfu. So I can’t go any further to flash the board

RobertLorincz, 2024-09-08:
I recommend going through the documentation and flash klipper if its not already flashed on the micro.

Naclifford, 2024-09-08:
After reinstalling klipper still no joy, so far it’s an expensive paperweight, I’m at a loss…

RobertLorincz, 2024-09-10:
hard to me to debug your issue, since I have no idea about your setup or how is the board connected. Some basic question, the toolboard power indicator LED is ON, correct?
You have the USB cables and power cables connected as shown in the connection diagram? Did you try other USB ports as well?

Closed 2024-09-14.

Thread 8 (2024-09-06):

Problem flashing klipper with katapult bootloader to SO2

jpapiez, 2024-09-06:
I want to install the Katapult bootloader to make it easy to update the klipper firmware, then deploy updates to klipper firmware via katapult. I flashed katapult with the following options:

Enable low-level configuration options
Micro-controller Architecture: STM32
Processor: STM32F042
Build Katapult deployment application (Do not build)
Clock Reference (8MHz crystal)
Communication interface: USB (on PA11/PA12)
Application start offset: 8KiB offset

Then I flashed Klipper with the following options:
Enable low-level configuration options
Micro-controller Architecture: STM32
Processor: STM32F042
Bootloader offset: 8KiB bootloader
Clock Reference (8MHz crystal)
Communication interface: USB (on PA11/PA12)
Optional features:
* Support GPIO "bit-banging" devices
* Support external sensor devices
* Support lis2dw 3-axis accelerometer

brunoR1000, 2024-09-06:
This might help you
https://bit.ly/3yXXzbX
Passcode: d5kp14h
You must have gcc compiler installed

RobertLorincz, 2024-09-08:
You did not mention your issue.
In the past, I tried this as well but there is not enough memory to do that in the STM32F042.

RobertLorincz, 2024-12-01:
Unfortunately, Katapult + Klipper do not fit into this microcontroller version; I'm working on a new toolboard version and using a bigger micro there.

RobertLorincz, 2024-12-01:
Unfortunately, Katapult + Klipper do not fit into this microcontroller version; I'm working on a new toolboard version and using a bigger micro there.

Closed 2024-12-01.

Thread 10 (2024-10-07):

Lost communication with MCU 'toolboard_t0'

dyocis, 2024-10-07:
I'm running RatRig V-Core4 500 with a Orbitool board.  I keep getting  lost communication error.   I've tried multiple toolboards, USB pcbs, and cables.  I ordered 3 toolboards, so I had 1 for IDEX and a spare.

It seems to work fine for 4 or 5 prints, then I get 3ish hours into a print and it shuts down due to "Lost communication with MCU 'toolboard_t0'" Then it does it every time I try to print something until I switch out the board or cable.  Then it will work fine for 4 or 5 prints.  I'm really stumped on this.  All the connectors are stock, I didn't crimp anything.  I've switched out previously removed boards and cables, and it will still print 4 or 5 prints without issue.

T/S info:

RatOS 2.1
Changed stock toolhead cables - I have rotated out 3 different stock cables
Changed USB cables - rotated out 3 stock cables, as well as a known good usb 3.1 cable
Verified 24v  - 24.3v while printing
Reported temp while printing: 70-75c
The VC4 part cooling fan draws air across board while printing, so there is a constant flow of air across the heatsink.

I can provide the klippy log, but it's too big to attach here.

RatOS.cfg:
[board_pins toolboard_t0]
mcu: toolboard_t0
aliases:
	#------------------------------------------- EXTRUDER motor pins --------------------------------------------
	e_step_pin=PB7,
	e_dir_pin=PB6,
	e_enable_pin=PB4,
	e_uart_pin=PB5,
	#----------------------------------------------- GENERAL PINS -----------------------------------------------
	e_heater_pin=PA0,
	e_sensor_pin=PA3,
	stepper_spi_mosi_pin=null,
	stepper_spi_miso_pin=null,
	stepper_spi_sclk_pin=null,
	adxl345_cs_pin=PA4,
	bltouch_sensor_pin=PA15,
	bltouch_control_pin=PB3,
	probe_pin=PA15,
	fan_part_cooling_pin=PA10,
	fan_toolhead_cooling_pin=PA9,
	fan_controller_board_pin=null,
	heater_bed_heating_pin=null,
	heater_bed_sensor_pin=null,
	4p_fan_part_cooling_pin=null,
	4p_fan_part_cooling_tach_pin=null,
	4p_toolhead_cooling_pin=null,
	4p_toolhead_cooling_tach_pin=null,
	4p_controller_board_pin=null,
	4p_controller_board_tach_pin=null

[mcu toolboard_t0]
serial: /dev/RatOS/ldo-orbitool-o2-t0

[temperature_sensor Orbitool_O2_T0]
sensor_type: temperature_mcu
sensor_mcu: toolboard_t0

[lis2dw toolboard_t0]
axes_map: x, z, y # Assumes back-facing vertical toolboard mounting
cs_pin: toolboard_t0:PA4
spi_bus: spi1

[extruder]
max_power: 0.995

[adc_temperature hotend_power_scale]
temperature1: 119
voltage1: 1.91
temperature2: 239
voltage2: 3.82

[fan]
max_power: 0.995

[heater_fan toolhead_cooling_fan]
# Use max_power: 0.5 for 12V, max_power: 1 for 24V (in printer.cfg)
max_power: 0.995
cycle_time: 0.0001

[output_pin O2_RUN_LED]
pin: toolboard_t0:PB8
shutdown_value: 0
value: 1

[temperature_sensor hotend_power_draw]
sensor_pin: toolboard_t0:PA2
sensor_type: hotend_power_scale

printer.cfg:

[fan]
shutdown_speed: 0.0
hardware_pwm: False
cycle_time: 0.0001
kick_start_time: 0.2
# off_below: 0.0
max_power: 0.995
#pin: toolboard_t0:PB1

[heater_fan toolhead_cooling_fan]
shutdown_speed: 0
tachometer_pin:toolboard_t0:PA8
tachometer_ppr: 2
tachometer_poll_interval: 0.0015

nickidotdk, 2024-10-25:
Hi @dyocis sorry to hijack this thread, but I am in the process of adding this board to my VCore. How did you wire the RatRig endstop to the board? Since there are only 2 pins, I guess the led feature of the endstop will not work when triggered. Is there anything else you had issues with installing this board?

Best regards

RobertLorincz, 2024-10-30:
can you share klipper log file?

winningfaith81, 2025-02-17:
I run into similar issues with disconnection from the toolboard. I have found that you must use the wire harness because as your printer is moving around the port that the cable connects to moves around. As I am in the process of building my only printer, I can't print one currently. I have used several zipties anchoring it to the Orbitor filament sensor and this has seemed to drastically improve my experience.

However, I have an issue where if I touch my hotend with something metal (let's say to change my nozzle) the board shuts down and gives a connection error. I wonder if this has something to do with having a Beacon probe? It sounds like the metal I'm introducing is shorting out the connection, but I'm not sure where/how.

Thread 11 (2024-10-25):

O2 PT1000 no selector in documentation

pmarkiewicz, 2024-10-25:
I'm looking to buy O2 toolboard, documentation states that it's compatible with PT1000 but I don't see any resistor selector for PT1000

RobertLorincz, 2024-10-29:
the selection is done only by klipper config

pmarkiewicz, 2024-11-01:
so there is no way to change resistor value? it's a pity as this heavily
reduces precision of PT1000.

regards

On Tue, Oct 29, 2024 at 10:45 AM LorinczElectronics <
***@***.***> wrote:

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

pmarkiewicz, 2024-11-04:
Good information, can you update documentation please?

On Mon, Nov 4, 2024 at 9:05 AM LorinczElectronics ***@***.***>
wrote:

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

pmarkiewicz, 2024-11-20:
just toolboard documentation that there is 2.2k resistor.

On Thu, Nov 7, 2024 at 9:43 AM LorinczElectronics ***@***.***>
wrote:

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

RobertLorincz, 2024-11-27:
It is written in the documentation check it...
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

Closed 2024-11-27.

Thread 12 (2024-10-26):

SO3 COmmunication issues.

Naveedy0, 2024-10-26:
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

Im sad and mad that I ever bought this.
Ever since I changed this, every once and a while it will ruin my print. Sometimes at the beginning other times mid print. Worst is after 12 hours printing time, where it suddenly stops communication.

I'm using a CB1 klipper setup on a Manta board.
I don't know what to do anymore.

RobertLorincz, 2024-10-30:
could you share with us klipper log file when this happens? Do you have the connection cable secured properly so it cannot disconnect itself?

Naveedy0, 2024-10-30:
I found out what the problem is. The o3 mcu gets crashes when the
temperature reaches 60+ degrees. It can't be cooled passively I had to add
a fan and change the steps from 32 to 16.

ons. 30. okt. 2024 08.34 skrev LorinczElectronics ***@***.***
>:

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

RobertLorincz, 2024-10-30:
The microstep setting should not influence the stepper driver temperature...16 or 32 should give the same value. Yes, temperature can be an issue; you could reduce stepper current. It also depends on how much air cooling you have in that region. Currently, we are also investigating this issue since the board is designed to work at higher temperature than 60°C. Mines are running fine at over 80 °C. It seems we got some bogus parts we use for the USB communication protection, which does not work well in hot environment as designed. If the issue persist we can try replace your unit.

Naveedy0, 2024-10-30:
I mean I would like a unit that could run passively.
My ambient temperature is 24 degrees, when I bought it I had a
understanding that that would be okay.

ons. 30. okt. 2024 09.04 skrev LorinczElectronics ***@***.***
>:

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

Naveedy0, 2024-10-31:
I tried again, 16 steps, no fan and the temperature reached 64 degree and
it stopped SO3.

Den tors. 31. okt. 2024 kl. 19.58 skrev Naveed Yousaf ***@***.***>:

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
>>> The microstep setting should not influence the stepper driver
>>> temperature...16 or 32 should give the same value. Yes, temperature can be
>>> an issue; you could reduce stepper current. It also depends on how much air
>>> cooling you have in that region. Currently, we are also investigating this
>>> issue since the board is designed to work at higher temperature than 60°C.
>>> Mines are running fine at over 80 °C. It seems we got some bogus parts we
>>> use for the USB communication protection, which does not work well in hot
>>> environment as designed. If the issue persist we can try replace your unit.
>>>
>>> —
>>> Reply to this email directly, view it on GitHub
>>> <https://github.com/RobertLorincz/Orbiter-Toolboards/issues/12#issuecomment-2446110369>,
>>> or unsubscribe
>>> <https://github.com/notifications/unsubscribe-auth/BLVLCNQHZO3A7T5IX3XPRJ3Z6CHHJAVCNFSM6AAAAABQUUOCJKVHI2DSMVQWIX3LMV43OSLTON2WKQ3PNVWWK3TUHMZDINBWGEYTAMZWHE>
>>> .
>>> You are receiving this because you authored the thread.Message ID:
>>> ***@***.***>
>>>
>>

Naveedy0, 2024-10-31:
And this time, with 16 steps and fan on, and it still stopped working.
I can't use this :(

Den tors. 31. okt. 2024 kl. 20.30 skrev Naveed Yousaf ***@***.***>:

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
>>> I mean I would like a unit that could run passively.
>>> My ambient temperature is 24 degrees, when I bought it I had a
>>> understanding that that would be okay.
>>>
>>> ons. 30. okt. 2024 09.04 skrev LorinczElectronics <
>>> ***@***.***>:
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

Naveedy0, 2024-11-02:
I have decided to remove it and run the orbiter without the ldo.
It is completely useless.

tors. 31. okt. 2024 22.57 skrev Naveed Yousaf ***@***.***>:

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
>>> So I changed it back to 32steps. And the so3 lost communication again
>>> during print.
>>> This time it wasn't the temp that was the issue. I don't think it can
>>> maintain 32steps.
>>> I have attached the log file.
>>>
>>> Den ons. 30. okt. 2024 kl. 09.06 skrev Naveed Yousaf <
>>> ***@***.***>:
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

RobertLorincz, 2024-11-04:
you may contact your reseller and ask for a replacement. Your unit is probably defect.

thomasgalambos1, 2024-11-26:
I have the same problem..... it is installed on a sv08 and it did run for aprox 10 prints and now every print crashes the same way... The orbiter 3 is great at printing but the combo with the toolboard is useless...

Naveedy0, 2024-11-26:
> I have the same problem..... it is installed on a sv08 and it did run for aprox 10 prints and now every print crashes the same way... The orbiter 3 is great at printing but the combo with the toolboard is useless...

I returned mine and rewired everything.
The only issue is the mess of a wire other than that everything works now.

RobertLorincz, 2024-11-27:
We had some bad component batches related to the USB protection circuit. We are working to fix it. I can only recommend users who have such issues to check my wiring guides on the orbiterprojects webpage. Ask for a replacement board along with the small adapter board if that does not resolve the problem, as that might also be the cause.
One big influence can be the supply voltage for the small adapter board. Make sure it does have 5V power supply from the USB connector, not less. It is common that this issue is due to a bad 5V power supply performance; instability due to load current change will cause a communication crash. The new version of the adapter board will completely fix this issue, it will have its own 5V power supply and not rely on the voltage from the RPI which can be dirty.

Naveedy0, 2024-11-27:
> We had some bad component batches related to the USB protection circuit. We are working to fix it. I can only recommend users who have such issues to check my wiring guides on the orbiterprojects webpage. Ask for a replacement board along with the small adapter board if that does not resolve the problem, as that might also be the cause. One big influence can be the supply voltage for the small adapter board. Make sure it does have 5V power supply from the USB connector, not less. It is common that this issue is due to a bad 5V power supply performance; instability due to load current change will cause a communication crash. The new version of the adapter board will completely fix this issue, it will have its own 5V power supply and not rely on the voltage from the RPI which can be dirty.

Please tell when the new version gets released. Whats the name going to be of the new version?
- I would like to have a pretty printer again.

RobertLorincz, 2024-11-27:
We are having the first samples now. I could arrange for you to get a sample. For me at the moment, it is not super clear if the issue is on the toolboard or on the adapter board. We know we had a bad batch on one component in the USB protection circuit. But its not fully clear what reached customers. I have seen many issues where the actual printer setup caused the issue with the 5V supply of the adapter board. This is very tricky for users to spot. Would you be able to help us debug this more deeply? I could arrange for you a new adapter board with its own 5V power supply, and you may check if the issue still persists or not with the toolboard you have.
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
Naveedy0, 2024-11-27:
> We are having the first samples now. I could arrange for you to get a sample. For me at the moment, it is not super clear if the issue is on the toolboard or on the adapter board. We know we had a bad batch on one component in the USB protection circuit. But its not fully clear what reached customers. I have seen many issues where the actual printer setup caused the issue with the 5V supply of the adapter board. This is very tricky for users to spot. Would you be able to help us debug this more deeply? I could arrange for you a new adapter board with its own 5V power supply, and you may check if the issue still persists or not with the toolboard you have.

I would like to try it out as well. It would give me a peace of mind as well to know the reason behind why it wasn't working properly.

thomasgalambos1, 2024-11-30:
> > We are having the first samples now. I could arrange for you to get a sample. For me at the moment, it is not super clear if the issue is on the toolboard or on the adapter board. We know we had a bad batch on one component in the USB protection circuit. But its not fully clear what reached customers. I have seen many issues where the actual printer setup caused the issue with the 5V supply of the adapter board. This is very tricky for users to spot. Would you be able to help us debug this more deeply? I could arrange for you a new adapter board with its own 5V power supply, and you may check if the issue still persists or not with the toolboard you have.
>
> I am fine with that because except of this issue orbiter 3 and the toolboard deliver very best prints. I have the toolobard on sv08 which has a mks skpir base dboard but i also checked raspberry pi and have same situation

On a sv08 i wired the original cable (24v, gnd, d+,d-) from motherboard toolohead connector  which means no usb adapter board bentween orbiter toolboard and motherboard and i am still testing on a longer print BUT it looks like the toolboard mcu is constnant at 54C and no more crash so 90% sure that the usb adapter is the  problem .. but i also adjusted main power source to be exactly 24v.... (was little bit less) . At least on sv08 ... this is the situation

Naveedy0, 2024-11-30:
Will it help if I just added a little fan to cool down the usb adapter? Maybe it just gets to hot inside the kabinet?

RobertLorincz, 2024-12-01:
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

Yes, it is very possible you are correct. LDO discovered they have received a fake or bad batch of components that are used in the USB protection circuit. Replacing the adapter board solved the issue I confirmed in a few cases I checked.

thomasgalambos1, 2024-12-01:
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

Great, how can we  get a new adapter board?  I would also like to purchase several orbiter 3 and toolobards but now i am ... stuck because i don't know how to purchase the fixed version"

RobertLorincz, 2024-12-03:
The fixed adapter version will be out soon; you can request a free replacement from LDO or your reseller. I do my best to assist here.

cyablo, 2025-02-28:
> The fixed adapter version will be out soon; you can request a free replacement from LDO or your reseller. I do my best to assist here.

Does this also apply to the Orbitool o2? I had a hell of a time with prints stopping & RPi freezing, tried Kernel, cables, power supply and stuff and now after the latest freeze, the o2 doesn't even show up as as USB device and seems to be dead!

RobertLorincz, 2025-03-01:
Yes, since both have the same adapter board. if that does not solve the issue, you should request a replacement board.

RobertLorincz, 2025-03-07:
Yes, it applies to Orbiter O2 toolboard as well. In case you are experiencing the issues like you mention it also can be that the toolboard has some issues, please ask for a replacement board from your reseller, LDO will support fixing the issue.

Dr. Robert Lorincz

________________________________
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

supercrossed, 2025-03-10:
Hi Robert, just came across this thread and having the same issue - intermittent MCU disconnects with the O2, and now the nitehawk36. The nitehawk is the 'updated' release from earlier this year, and the USB board is different from the O2, it is about twice the size. Is this the updated version?

How could I request an updated 5v adapter board?

Closed 2025-03-10.

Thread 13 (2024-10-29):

Q maybe... findind default (must)    shutdown_value: 0.0   is BAD!

ptegler, 2024-10-29:
Klipper    issue??   seems flashing is an issue with anything other than   _shutdown_value: 0.0_    set.
this is NOT good...you should default to (hot end at a minimum) fans left on full power when the machine faults, to save clogs in the hot end from heat soak if the fan goes to zero when hot at fault.

RobertLorincz, 2024-10-30:
I'm not sure what you mean here...Klipper does not flash any configuration values...The HW design is done in a way that during shutdown the hotend fan is automatically enabled without software request. Software request value in shutdown only works if the micro is still alive; if not, then it does not do anything...hence we have the HW implementation instead of software config.

Closed 2025-01-16.

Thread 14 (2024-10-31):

Error temp measure

dimicel, 2024-10-31:
The thermistor I have installed was measuring the temperature correctly when connected to the board. With the OrbitertoolO2, and using the same configuration (replacing the pin with the tool's pin), it shows a very low temperature, around 3 degrees and a bit, when the ambient temperature is about 20 degrees.

RobertLorincz, 2024-11-04:
Have you configured the correct pull up resistor?

dimicel, 2024-11-04:
Ok, That was the problem. I had crossed that line. Thnaks

Closed 2024-11-04.

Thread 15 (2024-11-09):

FIlament runout on SO3 Toolboard not working

Luca432122, 2024-11-09:
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

I have not made any changes to the runout config but i keep getting the error "The value 'runout_filter' is not valid for ID"

Luca432122, 2024-11-10:
I've just noticed that runout is written "runout" in the switch definition and "runnout" in filament macros could that be the issue?

`#***********************************filament swicth definition***********************************************************

[filament_switch_sensor SO3Senzor]
switch_pin: SO3:PA13
pause_on_runout: False # do not change to true, printer is paused in the next sections
runout_gcode: UPDATE_DELAYED_GCODE ID=runout_filter DURATION=0.5 # duration defines the filter time for runnout detection
insert_gcode: filament_load_init
event_delay: 1.0
pause_delay: 0.1

#////////////////////////////////////////Filament Unload macros/////////////////////////////////////////////////

[gcode_button filament_unload]
pin: !SO3:PA10
release_gcode:  # filament unload procedure
  SET_LED LED=SO3RGB RED=0.0 GREEN=0.5 BLUE=0.5
  filament_unload_init
press_gcode: # do not add any macro call here

[delayed_gcode runnout_filter]
gcode: #checking if filament runout is still present after defined delay time, default 0.5s
  {% if printer["filament_switch_sensor SO3Senzor"].filament_detected==false %}
      runnout_init
  {% else %}
      M118 Runnout sensor intermitent contact detected!
  {% endif %}
`

Luca432122, 2024-11-10:
Happened due to this #1

RobertLorincz, 2024-12-01:
this bug is corrected in the new macro of the extruder.

RobertLorincz, 2024-12-01:
The new macro corrects this issue

Closed 2024-12-01.

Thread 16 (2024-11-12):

Orbitool O2 probe current

christianbundy, 2024-11-12:
The documentation indicates that the Orbitool O2 supports the BTT MicroProbe v2, but when I plug it in the probe only turns on the LED. When using other power sources, it turns on the LED and runs a self-test that actuates the servo three times.

What’s the max current for the probe 5V power? My multimeter seems to show ~0.4A, but the probe data sheet shows a max current of 3A. Is this a faulty Orbitool O2, or is the Orbitool incompatible with the MicroProbe v2? Or maybe something else?

smbenson0712, 2024-11-12:
After reviewing the first issue on S03 board and wiring the probe this way - Pin1 - Black, Pin2 - Red, Pin3 - Yellow, Pin4 - Black, and Pin5 - White (Like the pinout diagram with servo and probe swapped) and changing the servo pin to PA15 and Probe Pin to PB3 as suggested, I can get the probe to deploy on power up, but not do the full self test.  It will not retract the probe with the stow macro.  The end stop works as it should, open when deployed and triggered when stowed.  If I wire like Section 3.8, I get no probe movement on power up or via macro, leading me to believe that the PA15 is actually the servo pin.
This is very confusing as the silkscreen on the board shows pin 5 as gnd like section 3.8, The pinout shows ground as pin 4.  Can you please advise on correct wiring and pin configuration for the O2 toolboard.

christianbundy, 2024-11-13:
Thanks! For what it’s worth, my problem occurs even when the only pins connected are +5V and GND, and this is specifically the Orbitool O2. I appreciate the heads up on the similar problem, but for other issues (especially unrelated to these 2 pins or the Orbitool O2) it might be better to create a new issue so that it can be thoroughly documented and easy for others to find!

smbenson0712, 2024-11-13:
Noted.  I am also using the 02 board and having the same problem with power up self test.   My concern was also the wiring discrepancies in the docs  that may also be causing an issue.  Maybe we both have bad boards, as I have tested with 3 new probes, I would say it's not the probes.

christianbundy, 2024-11-13:
On Discord I saw someone say that they had the same problem with the MicroProbe with the Octopus board, which makes me wonder whether this is an issue with the BTT Microprobe requiring lots of current on startup rather than specifically an issue with the Orbitool. It isn't clear to me whether this is as simple as "the buck converter doesn't supply enough current" or whether there's some safety feature that's preventing the MicroProbe's high current draw. (Or, maybe it's something else entirely?)

Happy to test if you have any ideas, I have a bunch of capacitors laying around and thought maybe that would help maintain 5V as the current increases (if that's even the issue), but I'm not great with electronics.

christianbundy, 2024-11-13:
I've opened an issue in the MicroProbe issue describing the issue as well, but it isn't clear to me where the problem is: https://github.com/bigtreetech/MicroProbe/issues/38

christianbundy, 2024-11-14:
I measured with a multimeter today, and when I hook my 5V power supply up to the probe it pulls 2A to deploy the servo. When using the Orbitool, I see a current draw of 0.15 mA, which makes me think it's an issue with the Orbitool rather than the probe.

smbenson0712, 2024-11-19:
I can confirm that the probe it not getting enough power.  It will self test when the probe is in the horizontal or probe up position. When the probe is facing the bed it will not self test completely.  It will deploy, but can't get enough power to retract.  According to the BTT documentation, the probe only requires 350mA to operate , what is the max 5V output from your board on the probe servo pin?

norston, 2024-11-19:
I am having exactly the same issue as you smbenson0712. My microprobe will work just fine in a horizontal or upside down position. I discovered this by accident, BTW. When I was swapping the probe to my spare probe I didn't bother to connect it to the print head, so I was just holding it in my hand, and viola, it worked! My printer is a normal type printer in the sense that it requires the probe pointing downward at the print bed. This problem seems to indicate that the probe isn't getting enough current to lift the probe upwards in it's normal position. I measured my voltage and the circuit is getting 5v. I've tried a couple different Microprobes v2.0 and it's exactly the same issue. These same probes work just fine on my EBB42 in any position. I should also add that the probe is correctly triggering the end stop when the probe is actually able to deploy or retract.

Look, I'm not trying to hijack this issue but since smbenson0712 went down this path I felt compelled to respond. I'll now open my own issue in case this one gets closed.  Thank you.

christianbundy, 2024-11-21:
> According to the BTT documentation, the probe only requires 350mA to operate , what is the max 5V output from your board on the probe servo pin?

My memory is that plugging it in would start between 300 mA and 400 mA and then drop to around 200 mA, but I tried to test today and accidentally fried my board. I’m not sure how. I tried to power a small light bulb but kept getting 0A on my multimeter, and then the board popped and the magic smoke came out.

I’m not sure what happened, but West3D confirmed in Discord that they’d had a few other bug reports from the Orbitool not supporting the MicroProbe, so its unlikely that I’ll be actively working on this problem any longer. I’m out $45 and a too many hours of debugging, but hopefully my flailing around GitHub/Discord/etc at least helped make this problem more apparent.

Good luck y’all!

norston, 2024-11-21:
Thanks for going as far as you did Christian. Sorry to hear about your board. Does anyone have the actual circuit layout for this board?  I’m curious to see how they are bucking down the voltage to 5v. At this point in time I think we need Dr Lorincz to shed some light.

RobertLorincz, 2024-11-27:
The 5V power supply on the toolboard is designed for a constant 500mA load current. It can supply more for shorter time periods. The limitation is only the thermal limitation of the Buck coil and driver circuit. It can supply 1A from more than 1 second.
From my opinion, the issue is the microprobe itself, even if users have positive experience when connecting it to BTT boards.
I did purchase a microprobe, and I was not able to make it work reliably. Here are my findings and checks:
- Checked the 5V power supply can deliver enough current for the probe - result OK - measured with scope drop over the 5V power supply when deploying the probe;
- checked the probe output signal - result bad behavior - Orbitool have internal pull=up resistor of 10kOhm - the probe output is not able to correctly pull the signal to low logic level - I get something like 2V as low level logic. I disconnected the 10K resistor and only used the internal micro pull up - behavior improved, but still low level was about 1.5V not zero. This explains why the behavior on some BTT board is better. In general, its a very bad idea to use as pull up only the internal resitance of the micro which is realively high impedance. Also, direct connection without any protection circuit is a bad idea. - I'm sure btt boards will fail ESD and EMI immunity test on this function - I doubt they've have done it...or done it correctly...
- lastly the deploy force of the probe is very weak...many cases fails to deploy fully even when supplied and wired correctly - even when I directly connected it to microcontroller pins like on BTT boards.
- I checked the probe accuracy they claim - is nowhere near I have seen up to 0.2mm differences.
- lastly this was only one sample I have tested, maybe my sample was in the bad performance range I donno - however due to the above issues I mentioned, I do not support or recommend the usage of this probe. Simply because I cannot guarantee proper operation of it. I prefer not to support the probe than to remove all the protection features of the board to improve a litle but not fix it totally.

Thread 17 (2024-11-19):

Orbitool O2 not able to stow Microprobe 2.0 in when mounted in a vertical position!

norston, 2024-11-19:
My Biqu Microprobe 2.0 will deploy and stow just fine in a horizontal or upside down position, but not in a vertical position. I discovered this by accident, BTW. When I was swapping the probe to my spare probe I didn't bother to attach it to the print head, so I was just holding it in my hand, and viola, it worked in a horizontal position. My printer is a normal type printer in the sense that it requires the probe pointing downward at the print bed. This problem seems to indicate that the probe isn't getting enough current to lift the probe upwards while in its normal position. I measured my voltage and the circuit is getting 5v. I've tried a couple different Microprobes v2.0 and it's exactly the same issue. These same probes work just fine on my EBB42 in any position. I should also add that the probe is correctly triggering the end stop when the probe is actually able to deploy or retract.

RobertLorincz, 2024-11-27:
In trying to solve this issue and help users, I also bought a microprobe...The documentation shows how I managed to setup. However, I have to admit is not working well and I ditched this probe. The hardware design of the probe is very poor, mechannical and electronical as well. Sometimes was working sometimes not. I did connected it to my toolboard to my mainboard...same thing...different power supply...same thing...my conclusion of the investigation is that the microprobe is very unrealliable and does not work well.. Even when I manged to make it work well it leak precision...I honestly do not recoemnd to use that probe.

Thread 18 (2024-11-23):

Klipper Menuconfig Settings

grainiac, 2024-11-23:
@RobertLorincz is there a detailed description of the required options in menuconfig to select, in order to compile a fresh firmware for the STM32F042? It's very easy to end up with a ROM that won't fit on the MCU'S flash memory. Maybe I was just blind but I did't find. Thank you!

grainiac, 2024-11-23:
The error I am trying to fix is the following (it seems the MCUs need to be on the same version):

MCU Protocol error

This is frequently caused by running an older version of the
firmware on the MCU(s). Fix by recompiling and flashing the
firmware.

Your Klipper version is: v0.12.0-377-g9bd0d4757
MCU(s) which should be updated:
**orbitoolO2: Current version v0.12.0-155-g4cfa266e**
Up-to-date MCU(s):
**mcu: Current version v0.12.0-377-g9bd0d4757**

Once the underlying issue is corrected, use the "RESTART"
command to reload the config and restart the host software.

mcu 'orbitoolO2': Unable to extract params from: config_lis2dw

grainiac, 2024-11-23:
I made some progress and have the Orbiter2 with the Toolboard now working with the firmware that it shipped with: v0.12.0-155-g4cfa266e

I commented the accelerometer related blocks, after that it worked:

###########################################################################################
###################### Onboard accelerometer and resonance tester config ##################
###########################################################################################

#[lis2dw]
#cs_pin: orbitoolO2:PA4
#spi_bus: spi1
#axes_map: y, z, x

#[resonance_tester]
#accel_chip: lis2dw
#probe_points: 140,120,30  # XYZ head position for testing
#min_freq: 10
#max_freq: 200

RobertLorincz, 2024-11-27:
check the user manual; there is an explanation of how to compole klipper. Some unused features need to be deactivated to reduce the generated code size.

Closed 2025-01-16.

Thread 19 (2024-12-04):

How to run a 4028 fan with PWM input on the OS2?

briggs2025, 2024-12-04:
I would like to run a PWM input (three wire) 4028 part cooling fan. I have Tool Fan and Part Fan ports available. We could use either PB1 or PA10 for the PWM output (to the fan). I just need to know how to make one of these ports always on, in order to supply power to the fan. Anybody have success or experience with what I'm trying to do?

RobertLorincz, 2024-12-05:
Could you tell me which partfan type you plan? Usually 3 pin fans have GND, POWER and tacho...in this case, you can leave the tacho signal out or connect it to a spare input if you have, example an input from the BL_Touch sensor.

smbenson0712, 2024-12-10:
Great question briggs2025. I too want to use a 4028. Just to be clear, these can come in three wire in two flavors. One with a tach, or one with a PWM input. Or, you can get them four wire with all of the above. Looking forward to your response Mr Lorincz.

smbenson0712, 2024-12-10:
Need an always on power for these fans, convert Tool Fan or Part fan like you said. Then, make one of these ports output PWM signal to fan. Right?

smbenson0712, 2024-12-10:
Figured it out - Using the Tool Fan port for fan power positive and negative(PB1) and using Part Fan negative pin(PA10) for PWM of fan.  You need to compile the klipper firmware for the toolboard to include Pin PB1 as on at startup in the GPIO Pin section of make menuconfig.  Then use pin PA10 for your part cooling fan pin in klipper config file.

Traveler61, 2024-12-10:
Does the 4028 run full speed at power up and then once booted stop? I have the high speed 4 wire version.

briggs2025, 2024-12-10:
Worked great, thank you smbenson. Mine works great now. Runs full blast until firmware kicks in.

smbenson0712, 2024-12-10:
Traveler61 - the fan will run full speed until the firmware boots up and if you have the PWM pin configured like normal [fan], it will go to zero because that would be it's normal state as a part cooling fan.  I have modified my M106/M107 gcode and scaled the fan output, so that the slicer fan speeds are more normal - the fan only operates between 38%-100% in PWM mode, so the fan settings in the slicer are different.  If you have the 4 wire model with the tach, you could try and hook the 24V, Tach, Gnd to Part fan and PWM to Tool Fan.  Please note : I have not tried that as my fan doesn't have a tach wire.

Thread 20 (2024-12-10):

Support for 5V Fans

vidarw, 2024-12-10:
Is it viable to set the PWM configuration even lower to support 5V Delta fans recommended for the XOL toolhead?
https://github.com/Armchair-Heavy-Industries/Xol-Toolhead/blob/main/docs/BOM.md

effnZACK, 2025-08-11:
That isn't really a true statement, it has been well tested by the XOL guys. That the GDSTime 24v does not compare to the Delta 5V, many experience issues using them. With the Nitehawk SB toolhead I was able to pull 5V off of the LED, and control the fan with the ground, not sure if that solution would work with your toolhead or not.

GDSTime 2510 24v 12k RPM= 2.45 cfm
Delta 2510 5v 15k RPM= 4.3 cfm

Both rated for 70-75C chamber temp.

The only 24v 2510 fan that may be work well is the Berserker 24v which claims 5.86 cfm and 155C chamber temp.

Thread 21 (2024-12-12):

Updating Klipper firmware error

Cagle3545, 2024-12-12:
I am trying to update klipper on my Orbitool O2. I have klipper updated on all other usb devices and on my Pi and Leviathan. I am on klipper version v0.12.0-396-gb7233d11. This is the error message I am getting when I run dfu-util --list :dfu-util: Cannot open DFU device 0483:df11 found on devnum 12 (LIBUSB_ERROR_ACCESS). I can see the board is in DFU mode.  Any help is appriciated.

Cagle3545, 2024-12-12:
I tried to flash the board and this is the message I get in return

Voron@pi:~/klipper $ make flash FLASH_DEVICE=0483:df11
  Linking out/klipper.elf
/usr/lib/gcc/arm-none-eabi/12.2.1/../../../arm-none-eabi/bin/ld: out/klipper.elf section `.text' will not fit in region `rom'
/usr/lib/gcc/arm-none-eabi/12.2.1/../../../arm-none-eabi/bin/ld: region `rom' overflowed by 385 bytes
collect2: error: ld returned 1 exit status
make: *** [Makefile:73: out/klipper.elf] Error 1

Cagle3545, 2024-12-13:
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

The guide shows support external sensor devices, can the guide be updated to reflect what is needed to be selected.

RobertLorincz, 2024-12-14:
There are changes in the Klipper config optional features section. I will update the documentation soon. Until then, just activate only the features I suggest in the current documentation and deactivate all the rest.

Closed 2025-01-16.

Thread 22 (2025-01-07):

Flash issue

Muttley65, 2025-01-07:
Hi guys , Orbiter2 Toolboard , after flash device it result hide or missing .
Is there something wrong ?

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

Muttley65, 2025-01-07:
Hi guys i resolved issue , i choosen wrong comunication interface not USB (on PA11/PA12) .

Closed 2025-01-16.

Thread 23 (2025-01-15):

O2 not controlling extruder motor.

MisterMicc, 2025-01-15:
[tmc2209 extruder]
uart_pin: S03:PB5
interpolate: true
run_current: 0.85
hold_current: 0.1
sense_resistor: 0.110
stealthchop_threshold: 0
driver_TBL: 0
driver_HEND: 6
driver_HSTRT: 7
driver_TOFF: 4

new toolboard not spinning my motor.

please chime in if you have any ideas.

RobertLorincz, 2025-01-16:
Your configuration seems to be wrong; check the config file recommendation here:
https://github.com/RobertLorincz/Orbiter-Toolboards/blob/ff7b98a028c4b539d2e272a329198ad768093f6f/Orbiter%20O2%20Toolboard/Klipper%20Config/OrbitoolO2.cfg

MisterMicc, 2025-01-17:
> Your configuration seems to be wrong; check the config file recommendation here: https://github.com/RobertLorincz/Orbiter-Toolboards/blob/ff7b98a028c4b539d2e272a329198ad768093f6f/Orbiter%20O2%20Toolboard/Klipper%20Config/OrbitoolO2.cfg

Thank you, all sorted and printing.

Is it possible to use a bbt Eddy with this toolboard?
I cannot find anything in the documentation

gilbertorconde, 2025-03-17:
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

I don't think so. Eddy uses CAN or USB, so the tool board would need to be working with CAN (which it isn't) or have a USB expansion hub of some sort on the orbitool (again, it doesn't have one). You can do it by running the USB wires from your RPI (or whatever you are using) to the toolhead alongside to the orbitool USB wire.
Looks to me, the best approach would be to just run the data lines and grab the power (5v, gnd) from the probe pins on the orbitool

RobertLorincz, 2025-03-19:
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

Unfortunately, the current toolboard version does not support such sensors. You need to wire it sepparatelly to your mainboard.

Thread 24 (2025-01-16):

Manual does not indicate what type of connector the 4-pin hotend/thermistor is

m00dawg, 2025-01-16:
Just grabbed an SO3 board for my XOL toolhead build (along with an Orbiter 2). My kit was purchased from Fabreeko but it seems to be missing the connector needed to wire up the hotend and thermistor. The problem is I can't find anywhere what the connector is. Ideally the manual and wiring pinout diagram should include the connector types so folks are able to pick up additional connectors as required. Else folks like myself are kinda left guessing. I haven't been able to get a concrete answer on the connection when asking various Discords and things.

Adding the connector types as noted would be a great addition to what appears to be a fantastic toolhead board!

RobertLorincz, 2025-01-16:
Indeed, it is missing. I had the impression I had shown it in the block diagram, but is it wrong what is there? The connector is a molex microfit.
https://www.molex.com/en-us/products/connectors/wire-to-board-connectors/micro-fit-connectors

By the way, that toolboard is for Smart Orbiter 3 not for Orbiter 2. You can use it, but it is not optimized for the Orbiter 2 features, especially the Orbiter 2 sensor.

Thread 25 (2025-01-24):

CAN Version

0xUnkn0wN, 2025-01-24:
I would like to use this toolhead PCB directly with a CAN bus.

This version could be delivered without the extra board.

Maybe it is possible to use the current version with CAN, not sure about the connection to the onboard MCU.

RobertLorincz, 2025-02-03:
It's USB not CAN. CAN connection not possible with these boards.

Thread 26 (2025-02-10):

Request document with klipper firmware settings and caveats.

coldelectrons, 2025-02-10:
To compile Klipper firmware, certain things need to known:
- mcu type (stm32f042)
- clock reference (???)
- pins for communication interface (???)
- application start offset (???)

Shane-Gadsby, 2025-02-12:
It took me a hot minute to find them too, but it was actually in the manual: https://www.orbiterprojects.com/download/SO3/Orbitool%20SO3%20User%20Manual.pdf page:10

Karlauer, 2025-03-09:
The problem is that the documentation for the O2 and SO3 on github is outdated.

Document versions on github:
- SO3: 1.13
- O2: 1.12

A lot of vendors direct to the github for detailed documentation. After searching a lot I found newer document version for the O2 (Document version 1.2) as well. These include klipper configuration, but the screenshots on page 11 show the config for the SO3 board. Maybe there is a newer version I haven't found.

I found a shop that offers the O2 manual: https://cdn.shopify.com/s/files/1/0239/9287/files/Orbitool2_v2.72_Manual.pdf?v=1716243417

Pleaes update the documentation on github. Many sites point here for a setup guide.

RobertLorincz, 2025-03-11:
The documentation on Github is the latest. I cannot control what vendors are publishing on their website.

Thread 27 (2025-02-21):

SO2 Communication Issues

winningfaith81, 2025-02-21:
Greetings! I'm having a heck of a time trying to troubleshoot a problem I keep having with my Orbitool SO2 board when I'm losing communication to the board. For what it's worth, I have a humidity of about 30% in my house right now with it being winter and my heat is running.

### **The Error:**
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

### **What I'm Doing:**
- Example 1: I'm working on my printer to calibrate my print settings. I go to wipe off excess filament from the hot nozzle with my metal scraper or metal tweezers post print. The printer shuts down and throws the error.
- Example 2: I need to measure the standoffs I'm using between the Orbiter v2.0 and the Orbitool board. I've got my digital calipers out and I'm measuring the length, touching one side to another. The printer shuts down and throws the error.
- Example 3: I'm installing the aluminum camera mount to the outside of my aluminum enclosure. The printer shuts down and throws the error.
- Example 4: I've taken off the Beacon probe. I was trying to get the error to pop. I reached down to home XY and just before or AS I was touching the LCD, the printer shuts down and throws the error.

### **What I DON'T Experience:**
I have left the printer on for hours and hours, not using it. I have never witnessed the printer randomly giving the error. It has always happened while I was touching it in some manner.

### **Troubleshooting:**

1. Checked the ground - I am grounded in all of my electronics into the aluminum frame and to the earth connection that runs into the power from my house. I think I might have two points grounded into the frame, so perhaps this is an issue - creating a cyclical route?? I'm not an electrician. I did verify continuity from the earth ground prong on the IEC inlet with various points in my build like a screw that is put directly into the end center tap of an extrusion, my headed bed ground point, and both of the points where I have grounds screwed on to the frame. All points have continuity.
2. I have a Beacon probe. I thought perhaps its operation was causing electrical disturbance and me touching the hotend with something metal was causing a short. I disconnected the beacon and messed around with the printer again. Still get a communication loss.

### **Hardware Setup:**
- Zero G CoreXY printer.
- Frame - Aluminum powder coated frames from DLLPDF.com
- Hotend - Phaetus Dragonfly BMO
- Extruder - Orbiter v2.0 with the v2.5 Upgrade kit
- Filament Sensor - Orbiter Filament Sensor v2 w/ tangle detect
- Toolboard: Orbitool SO2 with stock, unmodified comm cable connected to supplied USB adapter board, connected with stock USB cable to RPi 5 for communication and directly to PSU for power. (For what it's worth, this board does not yet have the 3D printed mount yet. It is screwed directly into frame extrusion.
- Probe - Beacon Rev H Low profile, connected with unmodified comm cable connected directly to RPi5

### **My Printer File**
[printer-config.txt](https://github.com/user-attachments/files/18913664/printer-config.txt)

### **Logs**
Klippy Log that shows the error around 11:58am CST 02/21/2025
[klippy.log-02.21.2025-12.07pmCST.txt](https://github.com/user-attachments/files/18913634/klippy.log-02.21.2025-12.07pmCST.txt)

winningfaith81, 2025-02-21:
I wonder if perhaps my issue is similar to this issue with [the fake / bad parts in the USB adapter board](https://github.com/RobertLorincz/Orbiter-Toolboards/issues/12#issuecomment-2509734355) .... I purchased mine from KB3D on 12/17/2024.

cyablo, 2025-03-01:
Hi there, I have the exact same problem on my o2. I was already going crazy and changed the whole Raspberry + power supply and tried different kernels before finding this issue ticket.

RobertLorincz, 2025-03-01:
If the issue happens when touching the printer, it's probably some grounding issue. Have you connected printer GND to the frame and to the earth connection? Do you have maybe exposed wires onto which you can discharge? In some printers with metal parts in the carriages accumulate static charge, and that can discharge at some point, causing all kinds of unexplicable issues.
The second very important topic is to have a stable 5V supply voltage, since the 5V supply, which comes from the RPI USB connection, supplies the board protection electronics. If that 5V supply voltage is not stable or is actually lower than 5V will cause troubles. The latest adapter board design avoids this by having its own stable 5V supply voltage, so it is not influenced by external noise.

cyablo, 2025-03-01:
The issues happened randomly, sometimes after just a few layers, sometimes after hours, sometimes not at all. I never touched the printer. It also happens when printing unattended over night. But lately, it happens almost every print and on the first few layers.

I tried a few power supplies and monitored them with a Fnirsi FNB48 USB tester. The one I use now is stable at ~5,1V, so that also shouldn't be the problem.

Is the problem supply voltage related? Because I dind't change anything but the issue went way worse yesterday and I can't finish a single print since then. Some bad parts were mentioned.

cyablo, 2025-03-01:
Maybe worth mentioning: It's not unusual that the Pi freezes right after klipper tries connecting to the toolboard after booting. I though it was the Pi and changed that too but the problem was still present.

winningfaith81, 2025-03-02:
I've not noticed anything with Pi freezes.

Robert - I have the USB board wired directly into my power supply. Should I move it to one of the HE ports on my main board? I'm running a BTT Octopus MAX EZ board. My PSU is the stock one from my Ender 5 Pro, it's a clone of Meanwell, a LRS-350-24.

I have my ground running from the IEC power plug to a wago where it splits to another wago on either side of the electronics bay and grounds into frame. The far side of the printer is also grounded to the frame. The only wires with bare ends are the ones that go into the wagos.

RobertLorincz, 2025-03-02:
Your connections are OK. What I meant is the 5V supplied from the PI. via the USB cable... If that 5V is not stable or lower than 5V can cause issues.

cyablo, 2025-03-02:
It doesn't exactly crash. You can still see the Shell over HDMI and the blinking cursor, but the USB stack seems to crash because keyboard and ethernet stop working at this point, so I can't really tell what is going on when it happenes. Happens on RPI 2 and 3B+ but always boots fine if I pull the toolboard cable before booting the pi.

RobertLorincz, 2025-03-02:
It seems to me your issue is due to the RPI. I have also experienced issues when I used RPI 3A+, sometimes it was starting up with a communication timeout error; it was recovering just fine after commanding a firmware restart. Sems this is due to slow RPI, since this issue never happened to me with RPI4.

cyablo, 2025-03-02:
When the Pi freezes, it's when klipper tries to connect to the orbitool. There is nearly 0 load on the Pi at that time and a Pi 3 has plenty of power running Klipper. Even the Pi 2 I had before is good enough. The freezing also NEVER happens during print when the Pi has some real load. Only on first connection when the Pi boots.

Besides that, my main problem is this:
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

RobertLorincz, 2025-03-05:
I know it has quiet enough power to run klipper. I just state what we have observed. And this startup disconnection is more likely with RPI3 and below. I had the same experience; after switching to CM4 and RPI4, the issue was gone. Seems to be related to some kind of task management. It seems during startup some communication is delayed, causing the timeout, but honestly, this is just a theory we were thinking of and never had fount a real smoking gun proof, just obervation. In my opinion, the protocol is too sensitive, especially at startup. I would retry to connect before throwing an error, which would work because every time a manual restart is issued, the problem is solved.

cyablo, 2025-03-05:
Maybe that's the case, I've no RPi 4 >= at hand, so I can't test. maybe I'll try some x86 SFF PC as Klipper host this weekend, if I've got some time, just to see if that resolves the startup connection issue.

But that's a problem I can work around like you said. My main problem really is loosing the connection to the o2 during printing without interaction, like in my screenshot. My reseller I bought the toolboard from said he hasn't heard of an issue like this. What's the best way to contact LDO to get an confirmation that it's a known problem?

cyablo, 2025-03-12:
I shall get a new adapter board from LDO on friday. Will report if that fixes my problem.

dmitry-voronoff, 2025-03-20:
Hi, I have the exact same problem—completely random disconnections from the Orbitool. The GND connection is fine (tested), and the power supply is also fine (I even bought a powered USB hub). I've flashed the latest Klipper firmware onto the Orbitool, BTT Pi2 (not RPi), and Octopus Pro v1.1, so they all have identical Klipper versions. BTT Pi 2 is powered directly from power supply 24V (not usb). However, I’m still experiencing disconnections.

Please help. I can't print!

[klippy.log](https://github.com/user-attachments/files/19373673/klippy.3.log)
[moonraker.log](https://github.com/user-attachments/files/19373808/moonraker.2.log)

winningfaith81, 2025-03-20:
Something I found was that the port where the cable connects to the board might not be connected well enough. Mine came right off recently. I used my high temper solder gun and attached it back to the plate. Testing is still going on to see if the problem persists. 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

winningfaith81, 2025-03-22:
Additionally, you want to make sure you have some sort of cable strain relief in place, like the board mount that is provided by the creator. I feel that with all the movement, the main cable does not stay seated well at all. There is no catch mechanism between the port and the cable connector like Molex cables have. I think this paired with general movement of the toolhead (and a poorly soldered port) is going to give intermittent connection problems while printing, for sure.

dmitry-voronoff, 2025-03-22:
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

Here is my setup. I think it is completely fine.

cyablo, 2025-03-22:
Just to let you know, I got a new USB adapter board from LDO and I'm sorry to say that it does not work at all. The green LED lights up when connecting USB to the Raspberry, and the O2 Toolboard also powers up (the probe lights up, and the filament sensor initializes) when 24V is applied. However, there is no USB connection with this board—lsusb only shows the SKR E3 mainboard.

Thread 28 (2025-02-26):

RGB Leds not working when heater fan is running

The-JurB, 2025-02-26:
I have a voron dragonburner with a Orbitor V2.0, the Orbitor 2 Smart Sensort and the Orbitool O2 (yes i'm using everthing, very good products by the way!)

De dragonburner als has 2 nozzle leds and 1 logo led. The leds are connected to the Orbitool O2. In klipper i am using https://github.com/julianschill/klipper-led_effect as recommended by the dragonburner.

Everything works fine when the printer is idle. I can change colors of the leds, control them individually etc.
It works both fine with the klipper-led_effect macro's and manual setting of the OrbiLed in Fluidd.

However, when the heater fan is running, only the first led of the rgb-chain can be changed. The other 2 leds are not responding. When the heater fan is off, all the leds can be changed.
 This behaviour is the same voor using klipper-led_effect macro's and manual changing the OrbiLed color. Only the first led can be changed. In the klippy log, the following error shown when you update the leds: "Neopixel update did not succeed"

Led configuration in the OrbitoolO2.cfg:

[neopixel OrbiLED]
pin: orbitoolO2:PA1
chain_count: 3 #setup specific
color_order: GRB  #setup specific
initial_RED: 0.0
initial_GREEN: 0.0
initial_BLUE: 0.1

RobertLorincz, 2025-03-01:
Well, this is a strange issue. I personally had not this kind of issue, but sometimes I also have trouble updating colors. Looking into the details, I found out that the timings of signals generated by klipper are really at the edge. Sometimes, depending on the LED you are using, the pulses are even out of spek. We have to open a ticket to klipper developers to fix this...I had one friend who changed the default timings to correct ones, and the issue disappeared. Best would be to have the bit time configurable, as even though all of the leds are WS2812 different variants have slightly different timing requirements.

The-JurB, 2025-03-12:
Thanks for your reaction. Can you open a ticket? You know exactly what to put in their.

dkowis, 2025-04-12:
I have also run into this, with almost the exact setup.

 I have a stealthburner with a rainbowbarf LEDs (so there's 8 LEDs just in that logo, because bling!) and two nozzle LEDs, and the LEDs just wedge when that fan comes on.

I also see the klippy log "Neopixel update did not succeed." so yeah I think I'm in the same predicament.

https://forge.light.kow.is/3d-printing/v350_config/src/branch/main/conf/sb_leds.cfg#L59-L76

```
[neopixel sb_leds]
pin: orbitoolO2:PA1
chain_count: 10

color_order: GRB,GRB,GRB,GRB,GRB,GRB,GRB,GRB,GRBW,GRBW

initial_RED: 1.0
initial_GREEN: 0.45
initial_BLUE: 0.0
initial_WHITE: 0.0
```

gilbertorconde, 2025-05-15:
My leds start failing as described when i replaced my toolhead fan from a normal 2 pins 24v one to a 3 pins (tacho). I could always go back, but i think the 3th pin in my fan is more important than the leds. But would be cool to understand and fix this. I've an O2 as well. Now im using a 3010 axial fan dc24v from a creality k1

RobertLorincz, 2025-05-17:
I would say this is some kind of weird Klipper issue; the RGB LEDs have no feedback...klipper does not know what they are set...so if it gives an error, probably it was not able to configure it.

Lemaro2211, 2025-07-09:
I only have a USB camera and my two toolboards connected, and I'm running Klipper on a Dell Wyse 5070, so the USB bandwidth shouldn't be capped yet. I tried connecting another LED strip directly to my SKR 1.3, and the LEDs work better there — although still not 100%. The first LED is always on, and I can only set certain colors like blue or white. Basically, everything else doesn't work at all.

dkowis, 2025-07-09:
I can change LEDs usually, until the hotend fan fires up. As soon as that happens, I can no longer set the LEDs. I have to set up the stuff _before_ firing up the hotend. I can do animated things without any hotend fan running, and that seems to work reliably, but there's definitely some kind of timing issue happening when the toolhead is "busy."

I don't pretend to know enough about the guts of how all this works, I can only describe the symptoms.

Lemaro2211, 2025-07-09:
I am able to change the color of the strip connected to the SKR, even when the toolhead is heated and the fans are running.

dkowis, 2025-07-09:
Yeah, I have no symptoms on my other LED strips attached directly to my Octopus. They always worked, even when I had a toolhead directly attached to that board.

Lemaro2211, 2025-07-09:
@dkowis Lucky you! XD I don’t know what it is, but none of the LED strips I’ve tested with Klipper have worked properly. However, all of them work perfectly with WLED, so the LEDs themselves are fine.

RobertLorincz, 2025-07-17:
> Any updates on this? On my O2 Board, the LEDs are white all the time, and I can’t even turn them off. I love the board so far, but this is really annoying. I have tried changing the BIT_MAX_TIME bit with no luck. For some reason, the LEDs seem to have some sort of addressing — since my strip is 22 LEDs long, if I set it to 22, all of them light up, but if I set it to 6, only 6 light up.

I do not have any updates so far. It is strange you have that issue; in my case, I tested, and I can update RGB LED's even when the hotend is running. One thing pops up in your text: you are using 22 LED;s connected to the RGB output? I'm certain the toolboard onboard power supply is not able to drive so many LED's The supply current is limited to 0.5A max as written in the user manual. A typical RGB LED consumes 60 60mA when commanded max white - with 22 LEDs, this would mean 1.32A. I'm not aware of any bit time configuration possibility for Klipper; as far as I understand, this is hardcoded.... It would be nice if the bit time would be configurable so we can adapt the signals to different LEDs as I learned not all WS2812 versions have the same bit timing.

Lemaro2211, 2025-07-17:
I am using COB LEDs. They have a much higher LED density but are not as bright. The strip I bought has 200 LEDs per meter and draws 12 W/m, meaning a single LED only draws 5 mA, and the 22 should draw around 0.11 A. I thought that would be fine.

Lemaro2211, 2025-07-17:
Pushing the limit how? Power-wise, or is it a problem sending out the data packets to so many LEDs? Because I have a simple ESP32 controlling around 800 LEDs with no problem (WLED, just for reference).

RobertLorincz, 2025-07-25:
Indeed there is an issue in Klipper's RGB signal timing. The timing is hardcoded, and the default is not optimum for all RGB versions, and in addition, we do not get the same timing on different micros. In the RGB connector power supply line there is a current limiter. If the current is too high, it will reduce the supply voltage or enter into protection mode. To have a correct operation of the RGB signals, we need a stable power supply. This does not explain why the issue only appears when the hotend fan is ON...These circuits are completely separate and not even close to each other on the PCB board. Could it be you have some power supply wiring issues on the RGB LEDs? Maybe GND not connected correctly, or you have some GND loops?

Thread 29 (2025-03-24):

SO3 Toolboard Not Detected by Raspberry Pi

jjwb22101, 2025-03-24:
Brand new SO3, connected to 24V power and USB, is not being detected by my printer's raspberry pi. I run lsusb (or ls /dev/serial/by-id/) and the main board MCU shows up just fine (BTT Octopus), but there are no results indicating that the SO3 toolboard is detected at all. It's definitely receiving power, since I get green LEDs on both the toolboard itself and the adapter board, and the fan on the SO3 spins up to max speed.

I've tried connecting it to all four of the USB ports on the Pi (the main MCU shows up fine regardless of port), swapping around USB cables (again, no difference), and even just plugging it into a USB port on my laptop. No luck on any of those. Any suggestions?

RobertLorincz, 2025-03-24:
Have you tried re-programming the board, using the RESET and BOOT buttons?

jjwb22101, 2025-03-24:
Yup. No changes regardless of what combination of buttons I push. Doesn't show up regardless

jjwb22101, 2025-04-03:
Any suggestions on other things I could try? Or is the board likely DOA?

JoeTheTacoLord, 2025-04-19:
I am having this same exact issue, is there any update on this? I ordered a second tool board and still had the same issue, so I doubt its just DOA. Is there supposed to be any LED indication on the board when it enters DFU mode?

RobertLorincz, 2025-04-22:
There is no LED showing up when in DFU mode. Usually if you supply the board with the 24V and USB connected, the DFU mode shall show up. If it already has Klipper loaded, then it should respond with a serial number. And DFU mode can be activated by RESET and BOOT buttons. Press down both buttons, release RESET and after about 2-3 seconds, release BOOT. and the unit should be in DFU mode.

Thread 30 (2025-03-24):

All of a sudden, fans not working anymore on Orbitool O2

technik-gegg, 2025-03-24:
I'm currently working on my own tool changer upgrade, which will eventually be equipped with 4 independent tool heads. Hence, I bought 2 Orbitool O2 tool board kits.
I installed both of them and applied the example Klipper configuration file. I was able to do the first calibration steps, i.e. PID tuning on both successfully and even got some filament to extrude for the very first crude test.
After a couple of days while I was working on the printer, I went to calibrate the E-Steps for both extruders. While on the 1st one everything went as expected, on the 2nd one I got skipping steps because the nozzle got clogged. Evaluating the issue, I figured that this was because the hotend cooling fan wasn't spinning (anymore). So I checked my configuration first but everything was ok. After that I went and measured the voltages on the tool board. What I found is, that all of a sudden, the hotend fan spits out a constant 12V (although on a 24V system) after powering the machine.
On the other two (Tool Fan and Part Fan) nothing happens. These two I've configured as generic fans in order to be able to spin them up manually but no voltages whatsoever. Everything else on this tool board is working as it's supposed to (i.e. heater, thermistor, stepper motor and even the Neopixel LED).
Just to be sure, I flashed the tool board once again with the latest Klipper driver but to no avail. On a short visual check I didn't spot anything concerning (so no burned ICs or similar). I even checked the PCB traces for the Tool fan and everything seems just fine.
Is this a (maybe rare but) known issue?
Is there something I can do or check or is this tool board now dead and has to be replaced?

RobertLorincz, 2025-03-24:
Hi. It can be issues with the board; however, I cannot judge this based on your desciption. I assume you have different serial number set for the two boards, and pin configuration and MCU name is updated accordingly.

technik-gegg, 2025-03-25:
Robert,
thank you for your quick reply. I found the culprit and as always, it was sitting in front of the monitor :o)
After you mentioned the configuration, I checked it again.
Yes, I did rename all the sections, i.e. mcu became orbitoolO2_0 and orbitoolO2_1 / tool_fan_0 and tool_fan_1 but even though I looked over it probably a couple of hundred times, I somehow managed to overlook the [heater hotend_fan], which I didn't rename.
Just after starring at the config files for quite some time and comparing them side by side it eventually hit me... go figure!

I'm glad it's nothing wrong with the tool boards and I'm now able to continue my journey.
At least my post might be helpful for others facing similar issues in the future.

TG

Closed 2025-03-25.

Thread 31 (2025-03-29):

Orbitool cooling fins and BLTouch connector colliding with printer frame

mauho, 2025-03-29:
Hi. I just got the OrbiTool 2 and I really like the build quality and thoughts that went into it! Unfortunately I can not use it right away :)

After installing the tool board and crimping the connectors for the stepper and BLTouch, I found out that - with the given hardware - the cooler fins would collide with the frame on the left side, and the BLTouch connector would collide with the frame on the right side.

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

I could bend the connector pins for the BLTouch to a 90° angle to solve one problem. Also I could shorten the 2 Aluminium spacers to give just enough room for the cooler fins to pass the frame. The tolerances are still very tight. Another Option would be to create a thicker baseplate (Phaetus Hotend) for the necessary clearance.

My Ender 3V2 was working with the BeltEnder mod as well as the Apogee Toolhead until one of the stepper cables wore out - which is why I got the Orbitool board.

I apologise if I missed an Information that this combination would not work.
Best Regards M.

mauho, 2025-03-31:
i managed to set it up without the sensor in place

mauho, 2025-04-02:
Thank you for the reply.

I have the combination up and running again without the filament sensor module. There are ~2mm of clearance between the toolboard and the stepper. A temporary fan will help with the temperature until I can redesign and print a new base.

Closed 2025-03-31.

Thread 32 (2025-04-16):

Klipper "step_pin" error message

Pete2554, 2025-04-16:
I believe I have an issue with 3 of my 4  So3 circuit boards. In each case Klipper comes up with the error message " Option 'step_pin' is not valid in section extruder x". I have reinstalled the the configuration files for each extruder and have redone the DFU process. Figuring it might have something to do with the USB cables, I swapped out, in turn, each USB cable assembly including the pi to USB cable, power board along with the USB cable to the extruder circuit board from the working extruder. With each cable assembly swap the other extruders were commented out in printer.cfg. Everything points to an issue or defect with the extruder circuit boards. The boards are essentially brand-new and have only recently been installed.

Below is the relevant section from the Klippy log:

=======================
temperature_probe btt_eddy: No drift calibration configured, disabling temperature drift compensation
temperature_probe btt_eddy: registered drift compensation with probe [probe_eddy_current btt_eddy]
Config error
Traceback (most recent call last):
  File "/home/makertech/klipper/klippy/klippy.py", line 130, in _connect
    self._read_config()
  File "/home/makertech/klipper/klippy/klippy.py", line 127, in _read_config
    pconfig.check_unused_options(config)
  File "/home/makertech/klipper/klippy/configfile.py", line 497, in check_unused_options
    self.validate.check_unused(config.fileconfig)
  File "/home/makertech/klipper/klippy/configfile.py", line 446, in check_unused
    raise error("Option '%s' is not valid in section '%s'"
configparser.Error: Option 'step_pin' is not valid in section 'extruder3'
webhooks client 548070833408: New connection
webhooks client 548070833408: Client info {'program': 'Moonraker', 'version': 'v0.9.3-72-g7cdcca3'}
===============================

Thanks in advance and hoping you can help.

RobertLorincz, 2025-04-22:
Could you share your configuration? Out of the description, I cannot figure out what your issue is. It seems you have something misconfigured.

Pete2554, 2025-04-22:
Hi Robert,

Thank you for your reply.

As per your request please find attached one of the extruder configuration files that's producing the "step_pin" error message. I've also attached the complete Klippy log file just in case.

Best regards,
Pete

________________________________
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

RobertLorincz, 2025-04-23:
I cannot find the attachments, the klippy log is not interesting

Pete2554, 2025-04-23:
Hi Robert,

I forgot that email firewalls don't like configuration files. Please see the zipped attachment.

I assume the extruder configuration is the only one you need.

Best regards,
Pete

________________________________
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

Closed 2025-05-12.

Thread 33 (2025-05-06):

Where can I get a new cable from?

MackinsVII, 2025-05-06:
Is the cable proprietary or can I buy one off the shelf as I have somehow lost mine?

gilbertorconde, 2025-05-10:
I used a can cable from mellow with no issues. I think it is this one:
I just found this on AliExpress:

https://a.aliexpress.com/_EukIVLC

You just need to make the right connections on the USB to pi board. Buy the right connector and repin it.

If it has a pair for data and a pair for power it should work. I don't know about emi shielding. But that one worked for me

Closed 2025-05-08.

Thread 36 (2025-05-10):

orbitool02 with BTT Eddy coil

gilbertorconde, 2025-05-10:
I'm wondering if it's possible to use the i2c version of the BTT Eddy. Now I have a cartographer but would be nice to just have one USB cable on my umbilical.

I noticed the eddy-ng project added touch probing capabilities to these probes.
So if I could connect to i2c version directly to the probe pins of the orbitool I could have all of this with just one cable.

I still have a lot of investigation to do on the BTT Eddy side (make sure the i2c version can use touch, how accurate it is, how it is affected by thermal drift if at all, etc) but this would be a good start.

cyablo, 2025-05-15:
That would be cool, but as far as I know, the used pins for the Probe PA15 and PB3, don't offer I2C on the STM32F042 Microcontroller.

gilbertorconde, 2025-05-15:
but [here](https://github.com/RobertLorincz/Orbiter-Toolboards/tree/main/Orbiter%20O2S%20Toolboard) it says i2c for bed level sensing and scanning. Am i missunderstanding anything?

cyablo, 2025-05-16:
Oh, I didn't even notice there will be a o2s Version with I2C and USB aux. Great! I was looking into the NiteHawk for my 2nd printer because I also wanted to use an eddy probe. Maybe I'm gonna wait for the o2s now.

gilbertorconde, 2025-06-16:
> [@gilbertorconde](https://github.com/gilbertorconde) can you tell, which pin you used for sda and which for scl? Thanks. Unfortunally there are still no schematics for the O2 available.

Sure, im using these:
```
scl_pin: toolhead:PB3 # Servo signal port (Remember, dont use alias)
sda_pin: toolhead:PA15  # Limit signal port
```

But what do you mean by "unfortunally there are still no schematics for the O2 available"? dont you have the schematics in this repo? If you're trying to say that there's no documentation on how to use the probe in O2 i dont think it will ever be. But you can get there by yourself pretty easly. If you follow the documentation on the probe they have an example on how to use the pins from the bltouch, then you can check the documentation on the O2 board and match them.
For the O2 you actually dont need it cause i just gave them to you, but if you have any other board you wish to test is basially the same.

gilbertorconde, 2025-06-16:
oh, ok. i get your point, sure. Well, at least we know we can use the pandapi sensor one. Btw, i've been printing  reliably with the probe. Having no issues at all.
Important notes:
Pin alias won't work, apparently they seem working, no immediate failures, but when start using the probe it start failing.
The bed mesh can't be as detailed as with cartographer usb. I'm using 20x20 probe count. Seems to be the maximum. (with cartographer i was able to go as far as 50x50).

qOtXqi, 2025-06-22:
@gilbertorconde @cyablo
I can confirm the BTT Eddy Coil is working fine with the Orbitool O2 (non s).

`[probe_eddy_current btt_eddy]
i2c_mcu: orbitoolO2
i2c_software_scl_pin: orbitoolO2:PB3
i2c_software_sda_pin: orbitoolO2:PA15`

even a 50x50 rapid_scan with 200 mm/s is working.

gilbertorconde, 2025-06-22:
That's quite amazing. I really thought that wouldn't work. Now I'm considering switching it. Many tks for the config. Is there anything particularly different that needs to be done when flashing the board? (Any new entry on the optional features or so?)

qOtXqi, 2025-06-22:
@gilbertorconde
Your welcome. When flashing the OrbitoolO2 you need to enable the optional features
```
[*] Support communicating with external chips via I2C bus
[*]     Support software based I2C "bit-banging
[*] Support ldc1612 eddy current sensor
```
and whatever else you need.

cyablo, 2025-07-03:
Really cool that it's working. I also ordered an Eddy Coil to try myself (only got the USB Version lying around, waiting for the O2S to be released or a NH36 for me to buy). I didn't know software I2C in Klipper is already fully implemented and stable.

Did you experience any problems so far?

qOtXqi, 2025-07-03:
@cyablo No, none. Everything is working fine. Even the load on the Orbitool STM32F042x6 is comfortably far from 100% while scanning. It has a load of 65% and an awake time of 86%.

gilbertorconde, 2025-07-03:
> Really cool that it's working. I also ordered an Eddy Coil to try myself (only got the USB Version lying around, waiting for the O2S to be released or a NH36 for me to buy). I didn't know software I2C in Klipper is already fully implemented and stable.
>
> Did you experience any problems so far?

i've been using as well since the last message i posted here and its working flawless since. The best part is its working even better than the pandapi. More reliable and less resource hungry. With pandapi, whenever i do a full bedmesh scan my cameras stop working during the process so you can see how heavy it is. With the BTT eddy coil it just works.
After you set up all the things (the z-offset that works for you) it just works.
I find myself just sending jobs to my voron without even going to baby check the first layer.

Closed 2025-05-15.

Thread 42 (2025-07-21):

menuconfig Settings for Orbitool 2S with STM32F072

der-pw, 2025-07-21:
I just wanted also to ask for menuconfig settings. As I saw, that you have switched the µC-Type from STM32F042 to STM32F072.
In another thread it saids, it's in the user manual, maybe i'm blind, but I cannot find it.
https://github.com/RobertLorincz/Orbiter-Toolboards/tree/main/Orbiter%20O2S%20Toolboard/Documentations
Is it possible to add some informations in the documentation, like a screenshot of menuconfig?

Thanks
Patrick

der-pw, 2025-07-21:
Okay i'm a blind dumbhead! 🤦‍♂️😁

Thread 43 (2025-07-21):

extruder temperature over 230deg at start

ed-auvinet, 2025-07-21:
Hi there,

I just install the SO3 and its dedicated toolboard. Unfortunately even if the extruder heater if off, the extruder temperature sensor is reporting over 230 deg C and its move around this value along time but never get to room temperature as it should be.

Many thanks for your help,

Best regards,

ed-auvinet, 2025-07-21:
Dear all,

Just found my error,

I left an extruder config in the main printer.cfg.

I removed it and all went back to normal.

Yeah!

Closed 2025-07-21.

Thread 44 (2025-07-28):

O2S Toolboard Mount - Component interference

jmedlin, 2025-07-28:
There is a part of the printed adapter that interferes with a component on the back of the toolhead board.  I cut away a part on my test print to show it.  It’s also visible in the CAD.

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

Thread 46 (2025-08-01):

The board o2 does not work after reboot

Juri4, 2025-08-01:
After DFU flash board .
All work.
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

After any reboot or update settings.
board not work
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

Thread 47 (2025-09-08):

The O2S Strain relief model doesn't fit

schmidtw, 2025-09-08:
I downloaded the O2S strain relief model & it does not fit the board.  Components on the board are in the way - both in the model in the repo & in real life.

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

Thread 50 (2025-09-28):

Klipper menu configuration SO3

miso2176, 2025-09-28:
I have the problem that my klipper menu configuration has a different structure and I am therefore unable to integrate the temperature sensors.
Here is a screenshot of all the possible selection and as you can see, this is different than in the instructions:

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

My System:
RPI5 with bookworm v12, Klipper v0.13.0-272 and SO3

Need help,
Thanks

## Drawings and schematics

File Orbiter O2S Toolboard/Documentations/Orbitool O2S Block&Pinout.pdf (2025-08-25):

# Orbitool O2S block diagram

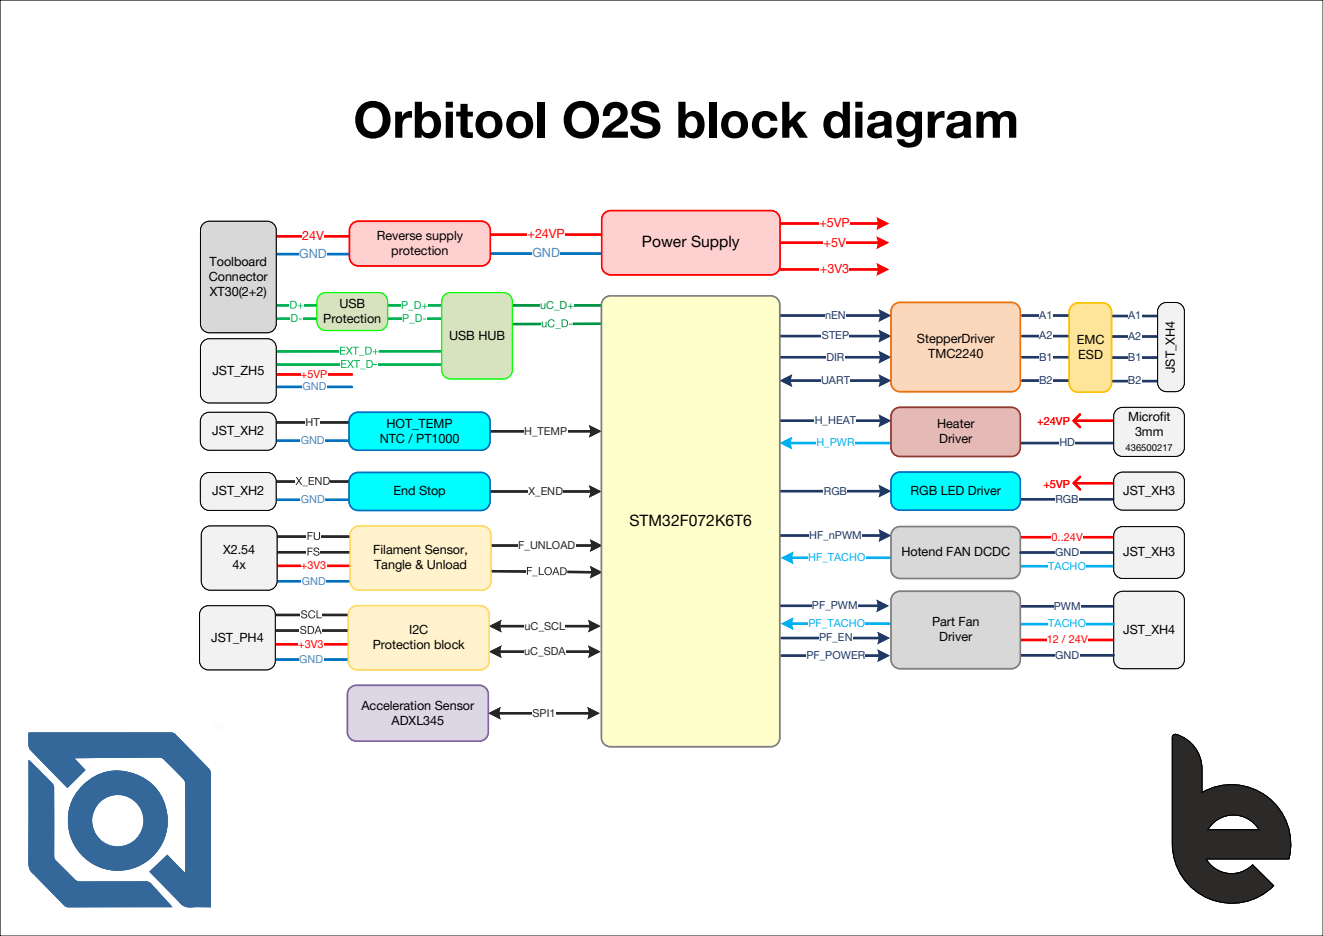
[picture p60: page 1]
nEN; STEP; DIR; UART; JST_XH4; EMC ESD; H_HEAT; H_PWR; Microfit; Heater Driver; StepperDriver TMC2240; RGB; +5VP RGB; HF_nPWM; HF_TACHO; TACHO; PF_PWM; PWM; JST_XH3; 24V GND; +24VP GND; GND; X_END; H_TEMP; F_UNLOAD; uC_SCL; uC_SDA GND; SPI1; Toolboard Connector XT30(2+2); JST_XH2; JST_PH4; Protection block; Filament Sensor, Tangle & Unload; End Stop; HOT_TEMP NTC / PT1000; Acceleration Sensor ADXL345; Reverse supply protection; Power Supply; +5VP GND; JST_ZH5; USB Protection; USB HUB; PF_TACHO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

RGB LED Driver

Hotend FAN DCDC

# Orbitool O2S pinout

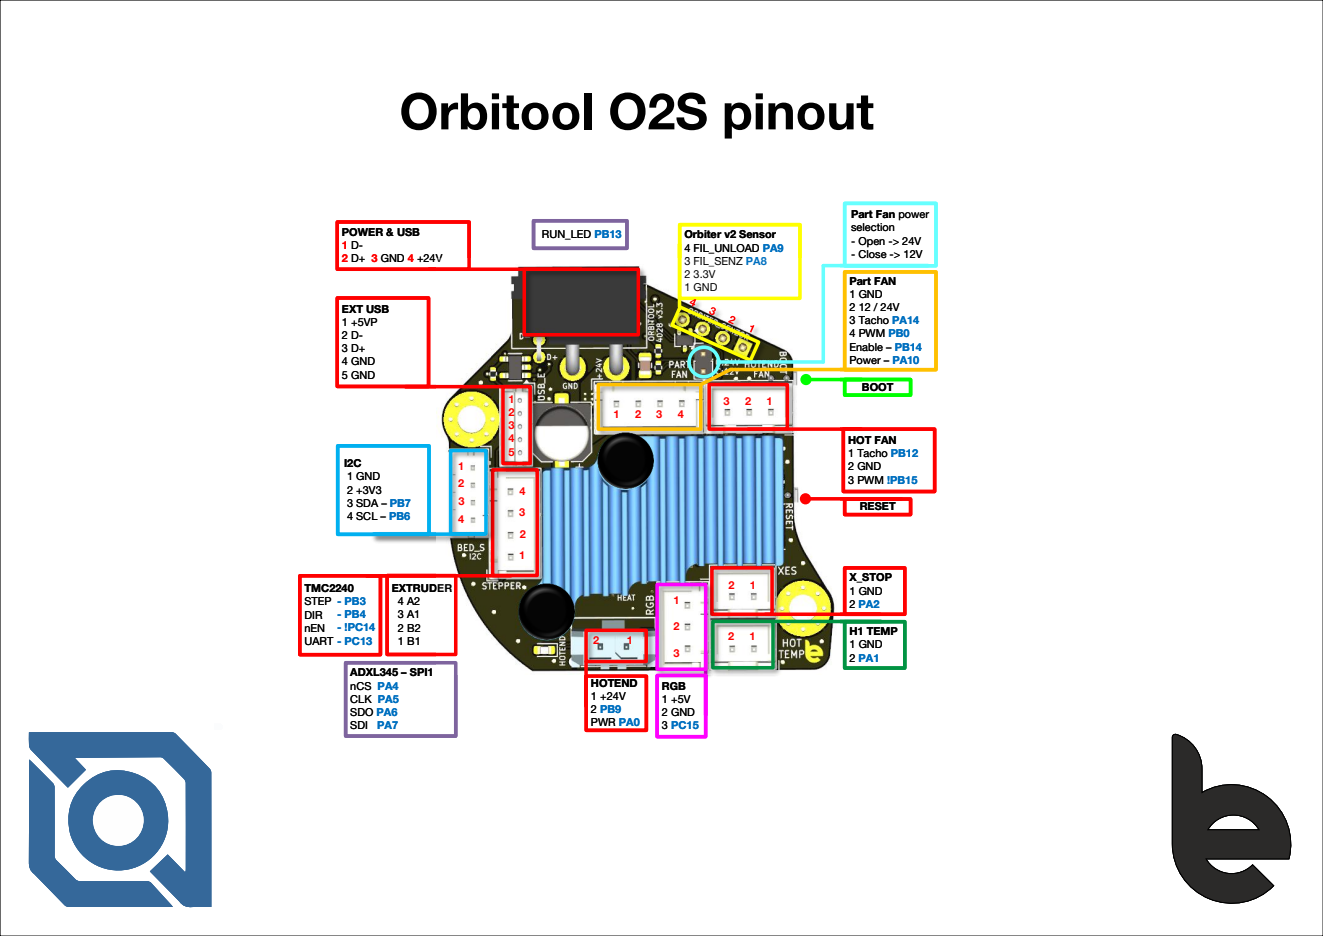
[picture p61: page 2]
Part FAN 1 GND 2 12 / 24V 3 Tacho PA14 4 PWM PB0 Enable – PB14 Power – PA10; HOT FAN 1 Tacho PB12 2 GND 3 PWM !PB15; EXTRUDER 4 A2 3 A1 2 B2 1 B1; TMC2240 STEP DIR nEN UART; EXT USB 1 +5VP 2 D- 3 D+ 4 GND 5 GND; X_STOP 1 GND 2 PA2; H1 TEMP 1 GND 2 PA1; RGB 1 +5V 2 GND 3 PC15; HOTEND 1 +24V 2 PB9 PWR PA0; Orbiter v2 Sensor 4 FIL_UNLOAD PA9 3 FIL_SENZ PA8 2 3.3V 1 GND; ADXL345 – SPI1 nCS PA4 CLK PA5 SDO PA6 SDI PA7; BOOT; RESET; POWER & USB 1 D- 2 D+ 3 GND 4 +24V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

Part Fan power
selection
- Open -> 24V
- Close -> 12V

# Orbitool O2S wiring

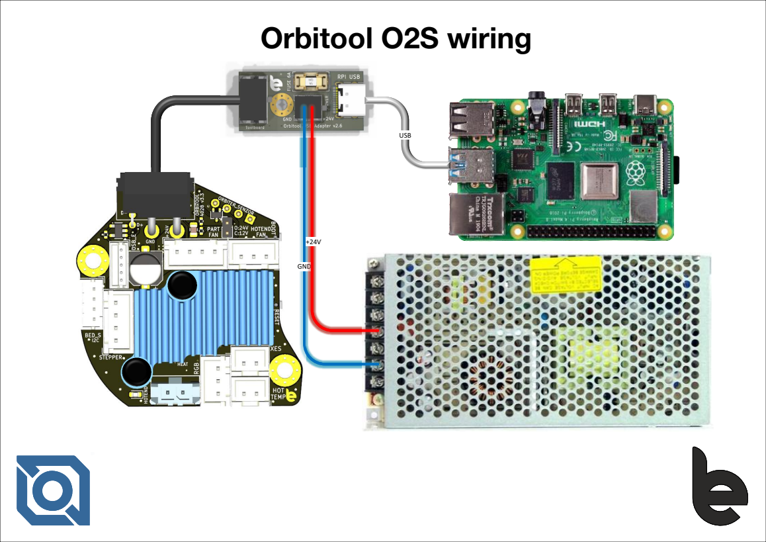
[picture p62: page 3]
GND; USB

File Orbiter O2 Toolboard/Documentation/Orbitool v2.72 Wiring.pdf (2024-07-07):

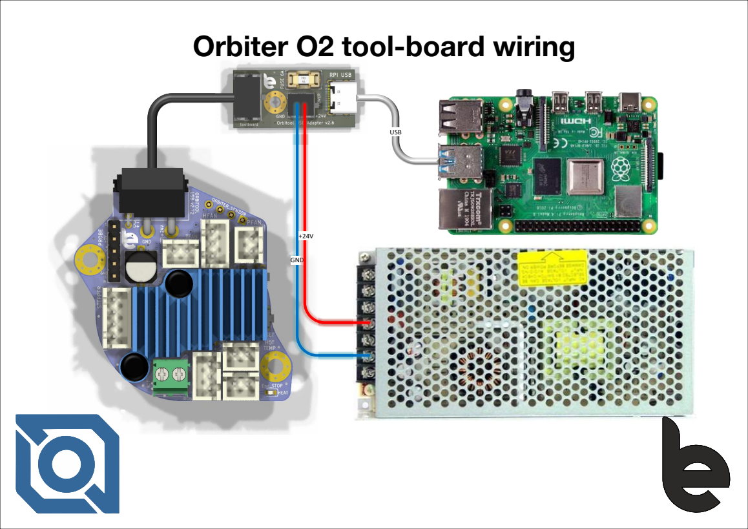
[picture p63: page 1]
GND; USB

Orbiter O2 tool-board wiring

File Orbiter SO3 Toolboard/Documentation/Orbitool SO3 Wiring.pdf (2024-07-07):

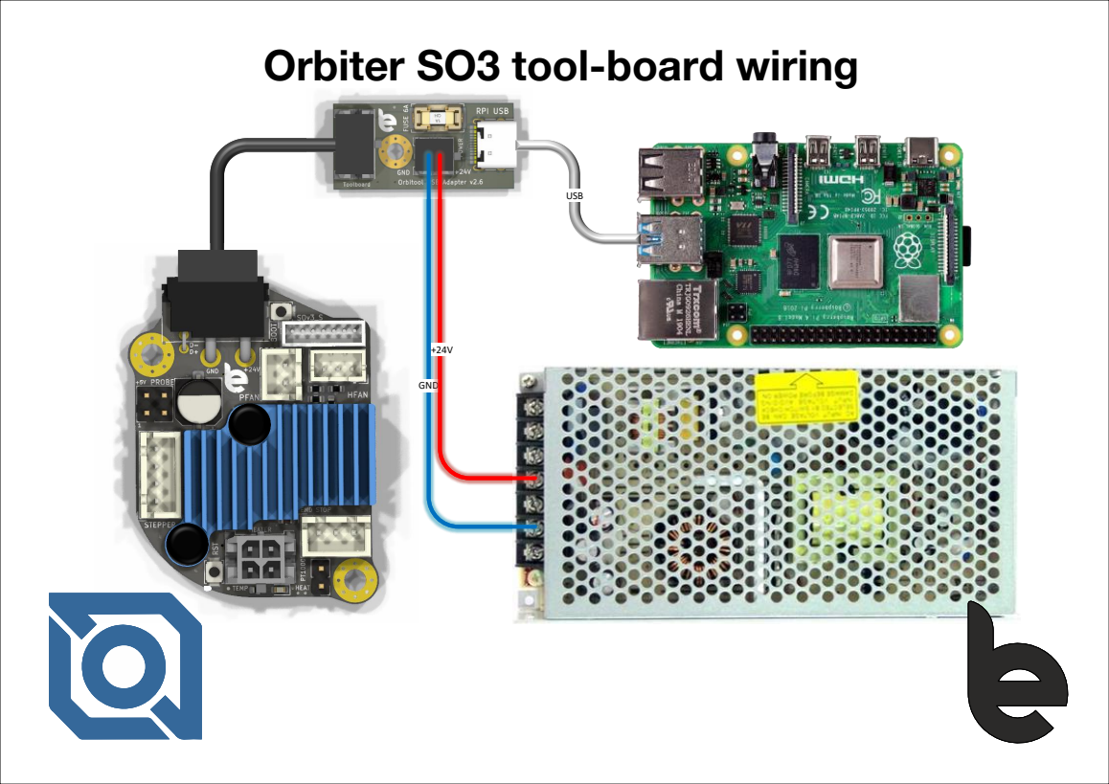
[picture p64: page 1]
GND; USB

Orbiter SO3 tool-board wiring

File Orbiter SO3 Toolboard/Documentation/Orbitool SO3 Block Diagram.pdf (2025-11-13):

# Orbiter SO3 tool-board block diagram

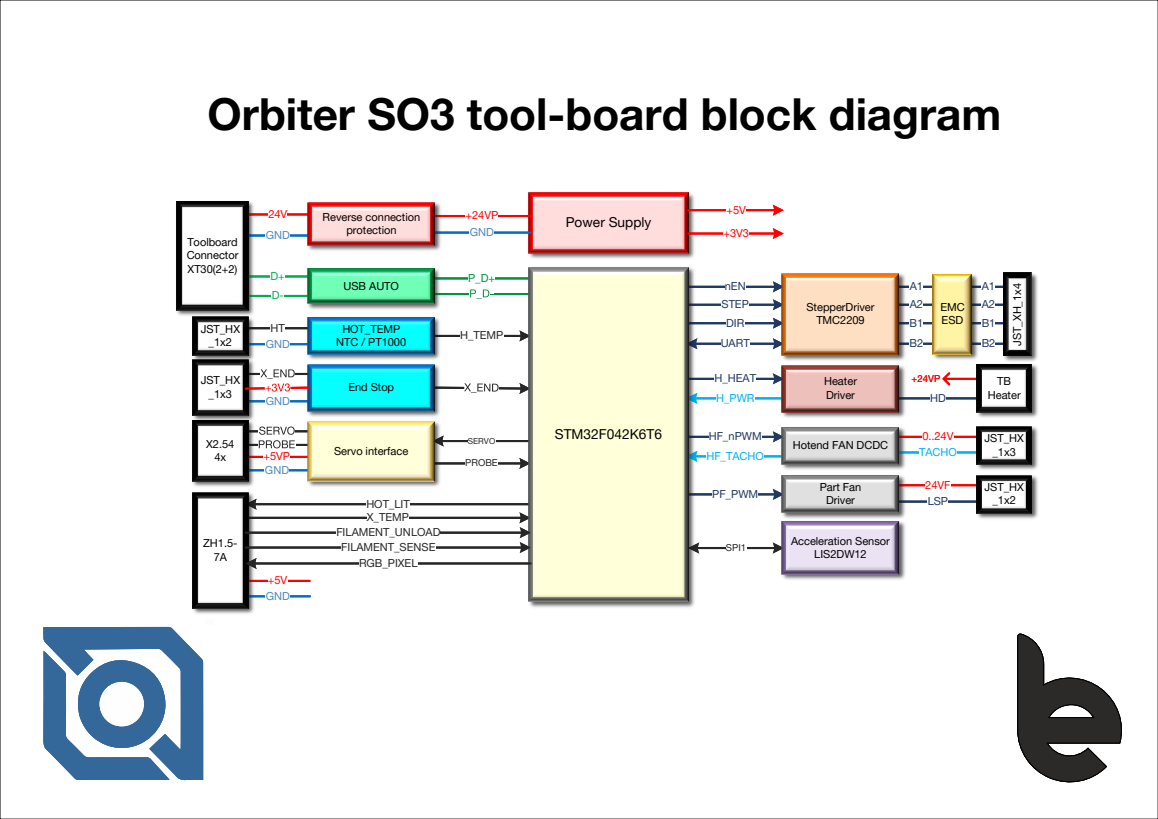
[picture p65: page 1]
Power Supply; nEN; STEP; DIR; UART; JST_XH_1x4; EMC ESD; H_HEAT; H_PWR; Heater; Heater Driver; StepperDriver TMC2209; HF_nPWM; HF_TACHO; 0..24V TACHO; PF_PWM; 24VF LSP; JST_HX _1x3; JST_HX _1x2; Part Fan Driver; GND; +24VP GND; HT GND; H_TEMP; HOT_LIT X_TEMP; SERVO; PROBE GND; SPI1; Toolboard Connector XT30(2+2); STM32F042K6T6; Servo interface; End Stop; HOT_TEMP NTC / PT1000; USB AUTO; Acceleration Sensor LIS2DW12; Reverse connection protection; FILAMENT_UNLOAD FILAMENT_SENSE RGB_PIXEL

Hotend FAN DCDC

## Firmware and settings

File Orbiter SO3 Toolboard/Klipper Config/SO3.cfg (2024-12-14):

#config file version v2.2.7
#release date: 14.12.2024

#Contributors: Lorincz Robert, Tomblarom

# PAUSE, RESUME and CANCEL macros are defined at the end of this config file.
# If you prefer using your own please delete them, otherwise define parking position below.
#when using PAUSE, RESUME and CANCEL macros of this file, please comment out the #[inlcude mainsail.cfg] from you printer.cfg file.

[mcu SO3]
serial: /dev/serial/by-id/usb-Klipper_stm32f042x6_SO3Tool-if00

#SO3 Tool-board pinout definition
# PA0 - Hotend heater control
# PA1 - Hotend power sensing input
# PA2 - Hotend temperature sensor input
# PA3 - Extruder fan Tacho input
# PA4 - LIS2DW12 nCS - SPI1
# PA5 - LIS2DW12 CLK
# PA6 - LIS2DW12 SDO
# PA7 - LIS2DW12 SDI
# PA8 - Extruder PWM fan speed control
# PA9 - Hotend lit LED control signal
# PA10 - Filament unload button
# PA11 - USB Data -
# PA12 - USB Data +
# PA13 - Filament sensor
# PA14 - Part fan PWM
# PA15 - Z sensor probe input

# PB0 - X end stop
# PB1 - extruder temperature
# PB3 - Z sensor servo output
# PB4 - TMC2209 nEN
# PB5 - TMC2209 UART
# PB6 - TMC2209 DIR
# PB7 - TMC2209 STEP
# PB8 - RGB LED

#################################################################################################################
################################ CHANGE HERE MACRO CONFIGURABLES ################################################
#################################################################################################################

[gcode_macro _SENSOR_VARIABLES]         # change here macro configurables, enable disable functions!*************************
variable_filament_load_temp     :230    # temperature to heat up hotend for filament loading, default is 235
variable_filament_unload_temp   :185    # temperature to heat up hotend for filament un-loading, default is 185
variable_filament_load_min_temp :190    # minimum hotend set temperature allowed in filament load macro, default is 190
variable_nozzle_purge_length    :100    # filament extrude amount during load sequenc, hotend purge from old filament, default is 100
variable_nozzle_purge_speed     :300    # filament extrude speed in mm/min adjust this value lower if flow is too high and extruder skips during loading, default is 300
variable_temp_restore           :True   # [True] restore previous temperature after filament change
variable_disable_autoload       :False  # disable filament autoload feature by setting this variable True
variable_disable_runout         :False  # disable runout by setting this variable True
variable_disable_autounload     :False  # disable auto unload filament by setting this variable to True
variable_pause_on_unload_button :True   # pauses the printer if the unload button is pressed during printing
variable_disable_runout_unload  :True   # disable auto filament unload after runout detection
variable_pause_timeout          :3600   # printer timeout setting in seconds, avoids disabling of steppers and heaters after klipper default timeout of 600s 
variable_enable_beep            :True   # uses M300 sound feature, set it True to enable
variable_park_position_x        :100    # edit your X parking position here for pause macro trigerred by runout
variable_park_position_y        :-5     # edit your Y parking position here for pause macro trigerred by runout
variable_park_lift_z            :10     # edit your Z lift amount for parking position here, default is 10
variable_park_retraction        :1      # edit your retraction amount for parking, default is 1
gcode:

[force_move]
enable_force_move: True

[respond]
default_type: echo

###########################################################################################
###################### Onboard accelerometer and resonance tester config ##################
###########################################################################################

[lis2dw]
cs_pin: SO3:PA4
spi_bus: spi1
axes_map: y, z, x

[resonance_tester]
accel_chip: lis2dw
probe_points: 140,120,30  # edit XYZ head position for testing
min_freq: 10
max_freq: 200

##################################################################
########################## EXTRUDER ##############################
##################################################################
[extruder]
step_pin: SO3:PB7
dir_pin: SO3:PB6
enable_pin: !SO3:PB4
microsteps: 32
full_steps_per_rotation: 200
#rotation_distance = <full_steps_per_rotation> * <microsteps> / <steps_per_mm>
rotation_distance: 4.69
nozzle_diameter: 0.400
filament_diameter: 1.750
max_extrude_only_distance: 2500
max_extrude_only_velocity: 120
max_extrude_only_accel: 3000
#_______________________ HEATER NOZZLE ____________________________
heater_pin: SO3:PA0
sensor_pin: SO3:PA2
#_________________________NOZZLE TEMP _____________________________
sensor_type: ATC Semitec 104NT-4-R025H42G  
pullup_resistor: 4700
min_temp: 0
max_temp: 300
pressure_advance: 0.015
pressure_advance_smooth_time: 0.03
min_extrude_temp: 170
smooth_time: 0.5
max_extrude_cross_section:10
max_power: 0.995
pwm_cycle_time: 0.01
control = pid
pid_Kp=24.859 
pid_Ki=2.072 
pid_Kd=74.578

[tmc2209 extruder] 
uart_pin: SO3:PB5
interpolate: true
run_current: 0.8
sense_resistor: 0.11
stealthchop_threshold: 0

[heater_fan extruder_Fan]
pin: !SO3:PA8
tachometer_pin: SO3:PA3
tachometer_ppr: 2
tachometer_poll_interval: 0.0005
heater: extruder
cycle_time: 0.0001 #10KHz PWM frecvency, do not change this!
heater_temp: 85
fan_speed: 0.65 # increase in case experiencing clogging during printing.
hardware_pwm: false
shutdown_speed: 0.0
max_power: 1.0

[firmware_retraction]
retract_length: 1.0
retract_speed: 100
unretract_extra_length: 0.0
unretract_speed: 80

[fan]
pin: SO3:PA14
max_power: 0.995
shutdown_speed: 0.0
cycle_time: 0.01
kick_start_time: 0.2
hardware_pwm: False

#################################################################################################################################
########################################### SO3 Features Configuration ##########################################################
#################################################################################################################################

[output_pin hot_lit]
pin: SO3:PA9
pwm: False
value: 1

[neopixel SO3RGB]
pin: SO3:PB8
chain_count: 1
color_order: GRB
initial_RED: 0.0
initial_GREEN: 1.0
initial_BLUE: 0.0

[thermistor SO3Thermistor]
temperature1: 25
resistance1: 100000
beta: 3950

[temperature_sensor SO3]
sensor_type: SO3Thermistor
sensor_pin: SO3:PB1
pullup_resistor: 4700
min_temp: 0
max_temp: 85

## STM32 MCU temp
[temperature_sensor SO3_MCU]
sensor_type: temperature_mcu
sensor_mcu: SO3

#################################################################################################################################
############################################## Runout and autoload macros #######################################################
#################################################################################################################################

#################################################################################################################################
####################################### DO NOT CHANGE ANYTHING BELOW THIS LINE!!! ###############################################
#################################################################################################################################
####################################### UNLESS YOU KNOW WHAT YOU ARE DOING OR YOU ARE BORED AND NEED TO DO SOMETHING OR YOU ARE ALONE AND NEED SOMETHING TO MESS UP YOUR LIFE OR YOU CAN DO IT BETTER THAN ME OR YOU ARE A REAL SMARTASS OR JUST BECAUSE YOU CAN OR YOU RUN OUT OF BEAR OR HAS NOTHING BETTER TO DO OR ANY UNREASONABLE REASON
#################################################################################################################################


#*****************************initial RGN LED set at printer start****************************************************************
[delayed_gcode startup_RGB_SET]
initial_duration: 2
gcode:    
  {% if printer["filament_switch_sensor SO3Sensor"].filament_detected==true %}
      SET_LED LED=SO3RGB RED=0.0 GREEN=1.0 BLUE=0.0
  {% else %}
      SET_LED LED=SO3RGB RED=1.0 GREEN=0.0 BLUE=0.0
  {% endif %}   


#***********************************filament swicth definition***********************************************************
[filament_switch_sensor SO3Sensor]
switch_pin: SO3:PA13
pause_on_runout: False # do not change to true, printer is paused in the next sections
runout_gcode: UPDATE_DELAYED_GCODE ID=runout_filter DURATION=0.5 # duration defines the filter time for runout detection
insert_gcode: filament_load_init
event_delay: 1.0
pause_delay: 0.1


#////////////////////////////////////////Filament Unload macros/////////////////////////////////////////////////
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

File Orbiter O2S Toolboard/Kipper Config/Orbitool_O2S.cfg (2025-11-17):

#################################################################################################################
################################## Orbittool O2S CONFIGURATION ##################################################
#################################################################################################################

#config file version v1.0.0
#release date: 17.07.2025


# End Stop pin PB0
# 24V ADC feedback pin PB1 - feature will be removed probably
# Z senzor Probe PB3
# Z Sensor servo PA15
# Orbiter filament sensor PA8
# Orbiter filament unload PA9


[mcu orbitoolO2S]
serial:/dev/serial/by-id/usb-Klipper_stm32f072xb_Orbitool_O2S-if00
restart_method: command

[extruder]
step_pin = orbitoolO2S:PB3
dir_pin = !orbitoolO2S:PB4
enable_pin = !orbitoolO2S:PC14
microsteps = 32
rotation_distance = 4.69 # Orbiter v2.5
full_steps_per_rotation = 200
nozzle_diameter = 0.400
filament_diameter = 1.750
heater_pin = orbitoolO2S:PB9
sensor_pin = orbitoolO2S:PA1
pullup_resistor = 2200
sensor_type = ATC Semitec 104GT-2 # update with correct sensor type PT1000 sensor are also suported
#sensor_type: PT1000
min_temp = 0
max_temp = 300 # increase in case your hottend suports higher operating temperature
pressure_advance = 0.015  # user calibration needed
pressure_advance_smooth_time = 0.03 # user calibration needed
max_extrude_only_distance = 500.0
max_extrude_cross_section = 20
min_extrude_temp = 20
smooth_time = 0.5
max_power: 0.995 # limit heater power to 99.5% to enable autorecovery from short detection
control = pid   # user calibration needed
pid_Kp=25.566 
pid_Ki=1.794 
pid_Kd=91.080


[tmc2240 extruder] 
uart_pin: orbitoolO2S:PC13
interpolate: false
run_current: 0.85 # Orbiter v2.5
rref: 12000
stealthchop_threshold: 0
#driver_TBL: 0
#driver_TOFF: 3
#driver_HEND: 8
#driver_HSTRT: 7

[stepper_x]
endstop_pin: orbitoolO2S:PA2

[heater_fan hotend_Fan]
pin: !orbitoolO2S:PB15  
tachometer_pin: orbitoolO2S:PB12
tachometer_ppr: 2
tachometer_poll_interval: 0.0005
heater: extruder
cycle_time: 0.0001 #10KHz PWM frecvency
heater_temp: 75
fan_speed: 1.0 # can be lowered to reduce fan noise
hardware_pwm: false
shutdown_speed: 0.0
max_power: 1.0 # can be lowered to reduce fan noise

[adc_temperature HOT_P]
temperature1:120 # value in Watts
#voltage1:1.32
voltage1:1.91 
temperature2:240 # value in Watts
voltage2:3.82 
#voltage2:2.64

[temperature_sensor Hotend_power]
sensor_pin: orbitoolO2S:PA0 
sensor_type: HOT_P


[firmware_retraction]
retract_length: 1.2 # user calibration needed
#   The length of filament (in mm) to retract when G10 is activated,
#   and to unretract when G11 is activated (but see
#   unretract_extra_length below). The default is 0 mm.
retract_speed: 120
#   The speed of retraction, in mm/s. The default is 20 mm/s.
unretract_extra_length: 0.0
#   The length (in mm) of *additional* filament to add when
#   unretracting.
unretract_speed: 120
#   The speed of unretraction, in mm/s. The default is 10 mm/s.

[neopixel OrbiLED]
pin: orbitoolO2S:PC15
chain_count: 2
color_order: GRB
initial_RED: 0.0
initial_GREEN: 0.0
initial_BLUE: 0.1

##############################################################
########### 2 and 3 wire part fan configuration ##############
##############################################################
# comment out this section when using the toolboard with 4 wire fan
# Warning make sure the FAN supply voltage selection jumper is in the right position - jumper must be closed for 12V fan type - open for 24V fan

[fan]
pin: !orbitoolO2S:PA10
enable_pin: orbitoolO2S:PB14
off_below: 0.2
tachometer_pin: orbitoolO2S:PA14
tachometer_ppr: 2
tachometer_poll_interval: 0.0005
shutdown_speed: 0.0
cycle_time: 0.0001 # 10KHz control signal frequency
kick_start_time: 0.2
hardware_pwm: False

##############################################################
########### 4 wire part fan configuration ####################
##############################################################
# comment out this section when using the toolboard with 2 or 3 wire fan
# Warning make sure the FAN supply voltage selection jumper is in the right position - jumper must be closed for 12V fan type - open for 24V fan

#[fan]
#pin: orbitoolO2S:PB0
#enable_pin: orbitoolO2S:PB14
#tachometer_pin: orbitoolO2S:PA14
#tachometer_ppr: 2
#tachometer_poll_interval: 0.0005
#shutdown_speed: 0.0
#cycle_time: 0.00004 # 25KHz control PWM frequency
#hardware_pwm: False



## STM32 MCU temp
[temperature_sensor toolboard]
sensor_type: temperature_mcu
sensor_mcu: orbitoolO2S

[output_pin T0_RUN_LED]
pin: orbitoolO2S:PB13
value: 1
shutdown_value: 0

##############################################################
################## Accelerometer Sensor ######################
##############################################################

[adxl345 Tool0]
cs_pin: orbitoolO2S:PA4
spi_bus: spi1
axes_map: y, z, x # Assumes back-faceing vertical toolboard mounting
spi_speed: 5000000

##############################################################
###################### Bed scanner ###########################
##############################################################
#configuration for I2C bed scanner based on LDC1612 

#[probe_eddy_current orbiscan]
#sensor_type: ldc1612
#i2c_mcu: orbitoolO2S
#i2c_bus: i2c1
#i2c_speed:100000
